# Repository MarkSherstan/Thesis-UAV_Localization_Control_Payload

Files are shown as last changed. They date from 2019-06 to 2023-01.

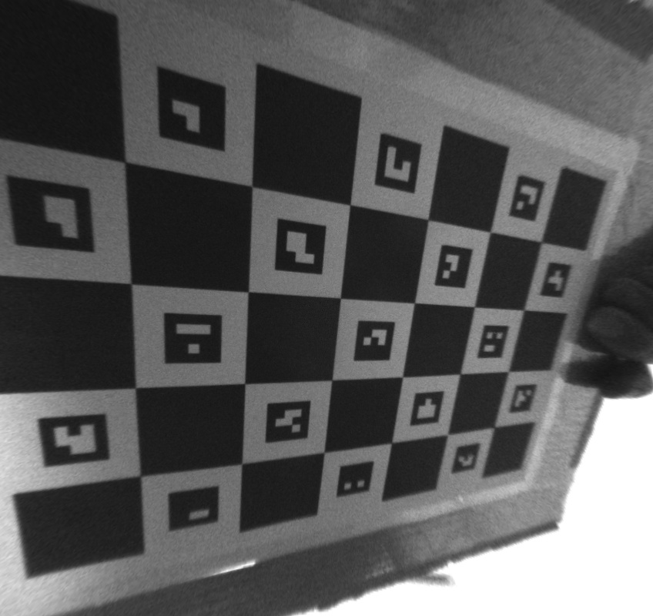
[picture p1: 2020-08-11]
control/cameraCalibration/calibrationImgs/Cam2/IMG_97.jpg

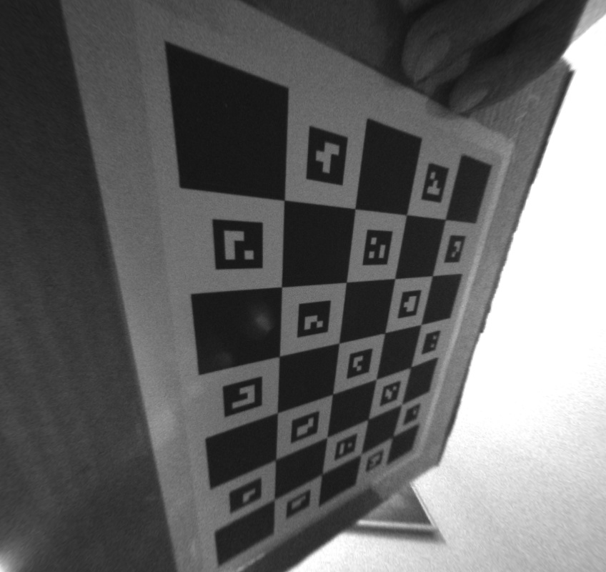
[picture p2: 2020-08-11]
control/cameraCalibration/calibrationImgs/Cam1/IMG_98.jpg

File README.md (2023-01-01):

# Thesis-UAV_Localization_Control_Payload
MSc thesis code for [Localization and Control of a Quadcopter Universal Payload System](https://era.library.ualberta.ca/items/3e5b67ea-13bb-48a5-877a-f02f7487af30).

## Abstract
There is a growing trend of using unmanned aerial vehicles (also known as UAVs, uncrewed aerial vehicles, or drones) to manipulate and interact with their surroundings. The algorithms and tools used are typically unique to the different tasks performed by UAVs; however, the fundamental UAV system largely remains consistent. This thesis offers a general quadrotor UAV system capable of performing multiple tasks dependent on available payloads. The system is empirically developed and performs localization using ArUco fiducial markers, an inertial measurement unit, and a Kalman filter. Navigation is achieved using a proportional integral derivative controller, and interfacing with various payloads is accomplished with a custom-developed universal payload manipulator. The system is described in detail and demonstrated with real-world experimentation, including the deployment of an example payload for removing twist caps off sump lubricant reservoirs. Empirical results show the developed system as an initial functional prototype in ideal conditions, and further work is required to increase system reliability and functionality for non-ideal scenarios.

## Setup
Clone the repo and install all the dependencies. For the first time call
`git submodule update --init --recursive`. Otherwise update using `git submodule update --recursive`.

Most of the developed code uses Python where a list of all the imported packages can be viewed in the below table. A majority of the Python packages come preinstalled; however, additional packages should be installed with `pip` (denoted with *). Two packages must be built directly from source code (denoted with **). All software ran on a Jetson Nano (quadcore ARM A57 processor) with Python 3.6.9 and Ubuntu 18.04.5 LTS.

| Package |Version | \| | Package |Version |
|---|---|----|---|---|
| datetime | 3.6.9  | \| | pymavlink* | 2.4.9  |
| DroneKit* | 2.9.2  | \| | pyrealsense2** | 2.36.0 |
| math | 3.6.9  | \| | pySerial* | 3.4 |
| Matplotlib* | 3.3.1  | \| | simdkalman* | 1.0.1  |
| multiprocessing | 3.6.9  | \| | statistics | 3.6.9  |
| NumPy* | 1.18.4 | \| | struct | 3.6.9  |
| openCV** | 4.3.0  | \| | threading | 3.6.9  |
| pandas* | 1.1.0  | \| | time | 3.6.9  |

For information regarding the building of non standard packages refer to the [wiki](https://github.com/MarkSherstan/UAV-Sampling-Control-System/wiki).
* [Build OpenCV](https://github.com/MarkSherstan/UAV-Sampling-Control-System/wiki/Build-OpenCV)
* [Build Pyrealsense2](https://github.com/MarkSherstan/UAV-Sampling-Control-System/wiki/Build-Pyrealsense2)

## Use  
Run the bash script `run.sh` and once the UAV is placed into `GUIDED_NOGPS` mode the UAV will be in full control. Use `control + c` to terminate the program and complete data logging.

## Flight Logs 
Flight logs are saved after each flight in `.csv` format. To plot data and analyze the log, navigate to the `/flightData` directory and enter the file name in the command line as such: `python3 plotter.py --input "flight1.csv"`.

## Payloads
Open the `/payloads` directory and navigate to either the `/cap` or `/MASTER` directory and build using PlatformIO. All pinout is labeled in `src/main.cpp`. The servo library may need to be re-installed with the following command: `pio lib install "Servo"` in the PlatformIO command line. Upload the compiled code to its respective PCB. 

## PCB
The PCB's were designed with [KiCad 5](https://kicad-pcb.org/download/) and manufactured by [JLCPCB](https://jlcpcb.com).

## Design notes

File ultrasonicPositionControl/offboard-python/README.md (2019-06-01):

# Off Board (Guided No GPS) Control Python
Python 2.7 is required. Python 3 and higher is not fully supported. The following packages should be installed (additional may be required, follow any errors generated).

```
sudo apt-get install python-lxml
pip install dronekit
pip install MAVProxy
pip install pymavlink
```

## Software In The Loop (SITL) Simulation
`dronekit-sitl` only has ArduCopter binaries up to version 3.3. As of May 2019 the ArduPilot GitHub repo has code up to 3.7-dev. Much of the current functionality from the new development is not captured in `dronekit-sitl` and therefore newer versions should be built to run an accurate simulation. The process outlined below primarily outlines the process for UNIX / MacOS operating systems, however links will be provided for other operating systems and more detailed instructions.

Start by cloning the [ArduPilot](https://github.com/ArduPilot/ardupilot) repo and navigate to new directory.

```
git clone https://github.com/ArduPilot/ardupilot.git
cd ardupilot/
```

Build the most up to date [binary](https://github.com/ArduPilot/ardupilot/blob/master/BUILD.md). Further information can be found as follows.
* [https://www.youtube.com/watch?v=PLGezPQYMrs&t=331s](https://www.youtube.com/watch?v=PLGezPQYMrs&t=331s)
* [https://www.youtube.com/watch?v=wLK2wLwEXm4&t=22s](https://www.youtube.com/watch?v=wLK2wLwEXm4&t=22s)
* [http://ardupilot.org/dev/docs/building-the-code.html](http://ardupilot.org/dev/docs/building-the-code.html)

```
git submodule update --init --recursive
./waf configure
./waf copter
```

Navigate to the following directory through the command line and run the simulator.

```
cd ardupilot/Tools/autotest
python sim_vehicle.py -v ArduCopter
```

Once the simulator is running. Open another command line and navigate to the following directory and run the program to test your control scheme.

```
cd UAV-Sampling-Control-System/ultrasonicPositionControl/offboard-python/
python main-SITL.py
```

## Off Board Interfacing
A [companion computer](http://ardupilot.org/dev/docs/companion-computers.html#companion-computers) is used to connect with the flight controller to implement off board control. Follow the guide for the respective hardware for setting up. To develop code connect on a desired serial port and use any of the commands outlined [here](https://web.archive.org/web/20180803235025/http://python.dronekit.io/guide/copter/guided_mode.html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).

Connect on `/dev/ttyS1` which are pins 8 and 10 on the J1 expansion connector of the Odroid C2. Further information can be found [here](https://wiki.odroid.com/odroid-c2/hardware/expansion_connectors) and a wiring diagram can be found [here](http://ardupilot.org/dev/_images/RaspberryPi_Pixhawk_wiring1.jpg) (RPi and Odroid C2 can be wired the same).

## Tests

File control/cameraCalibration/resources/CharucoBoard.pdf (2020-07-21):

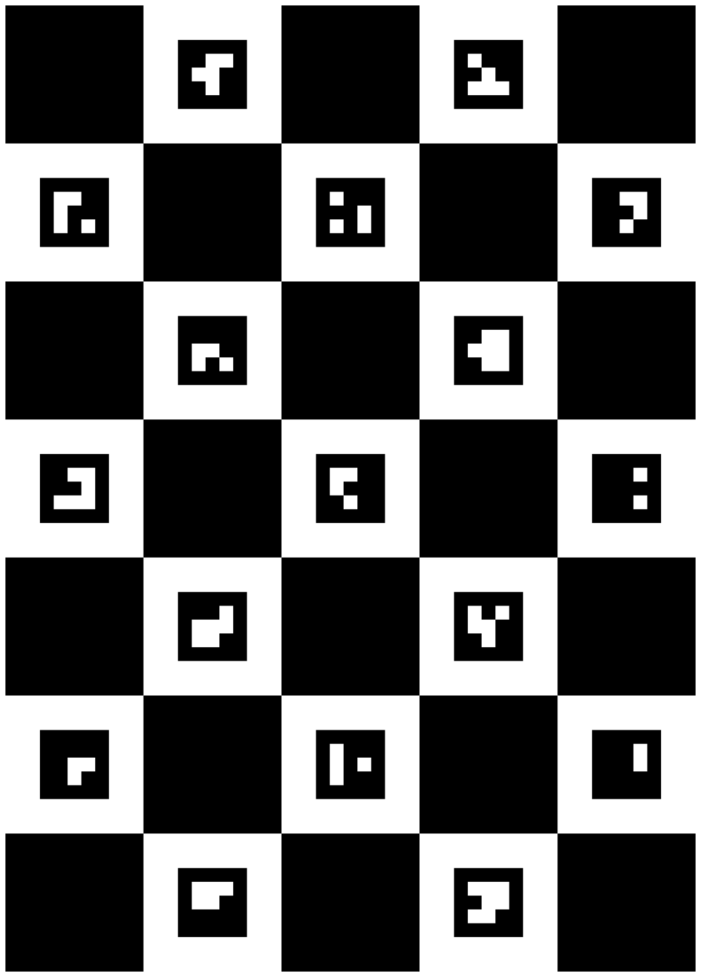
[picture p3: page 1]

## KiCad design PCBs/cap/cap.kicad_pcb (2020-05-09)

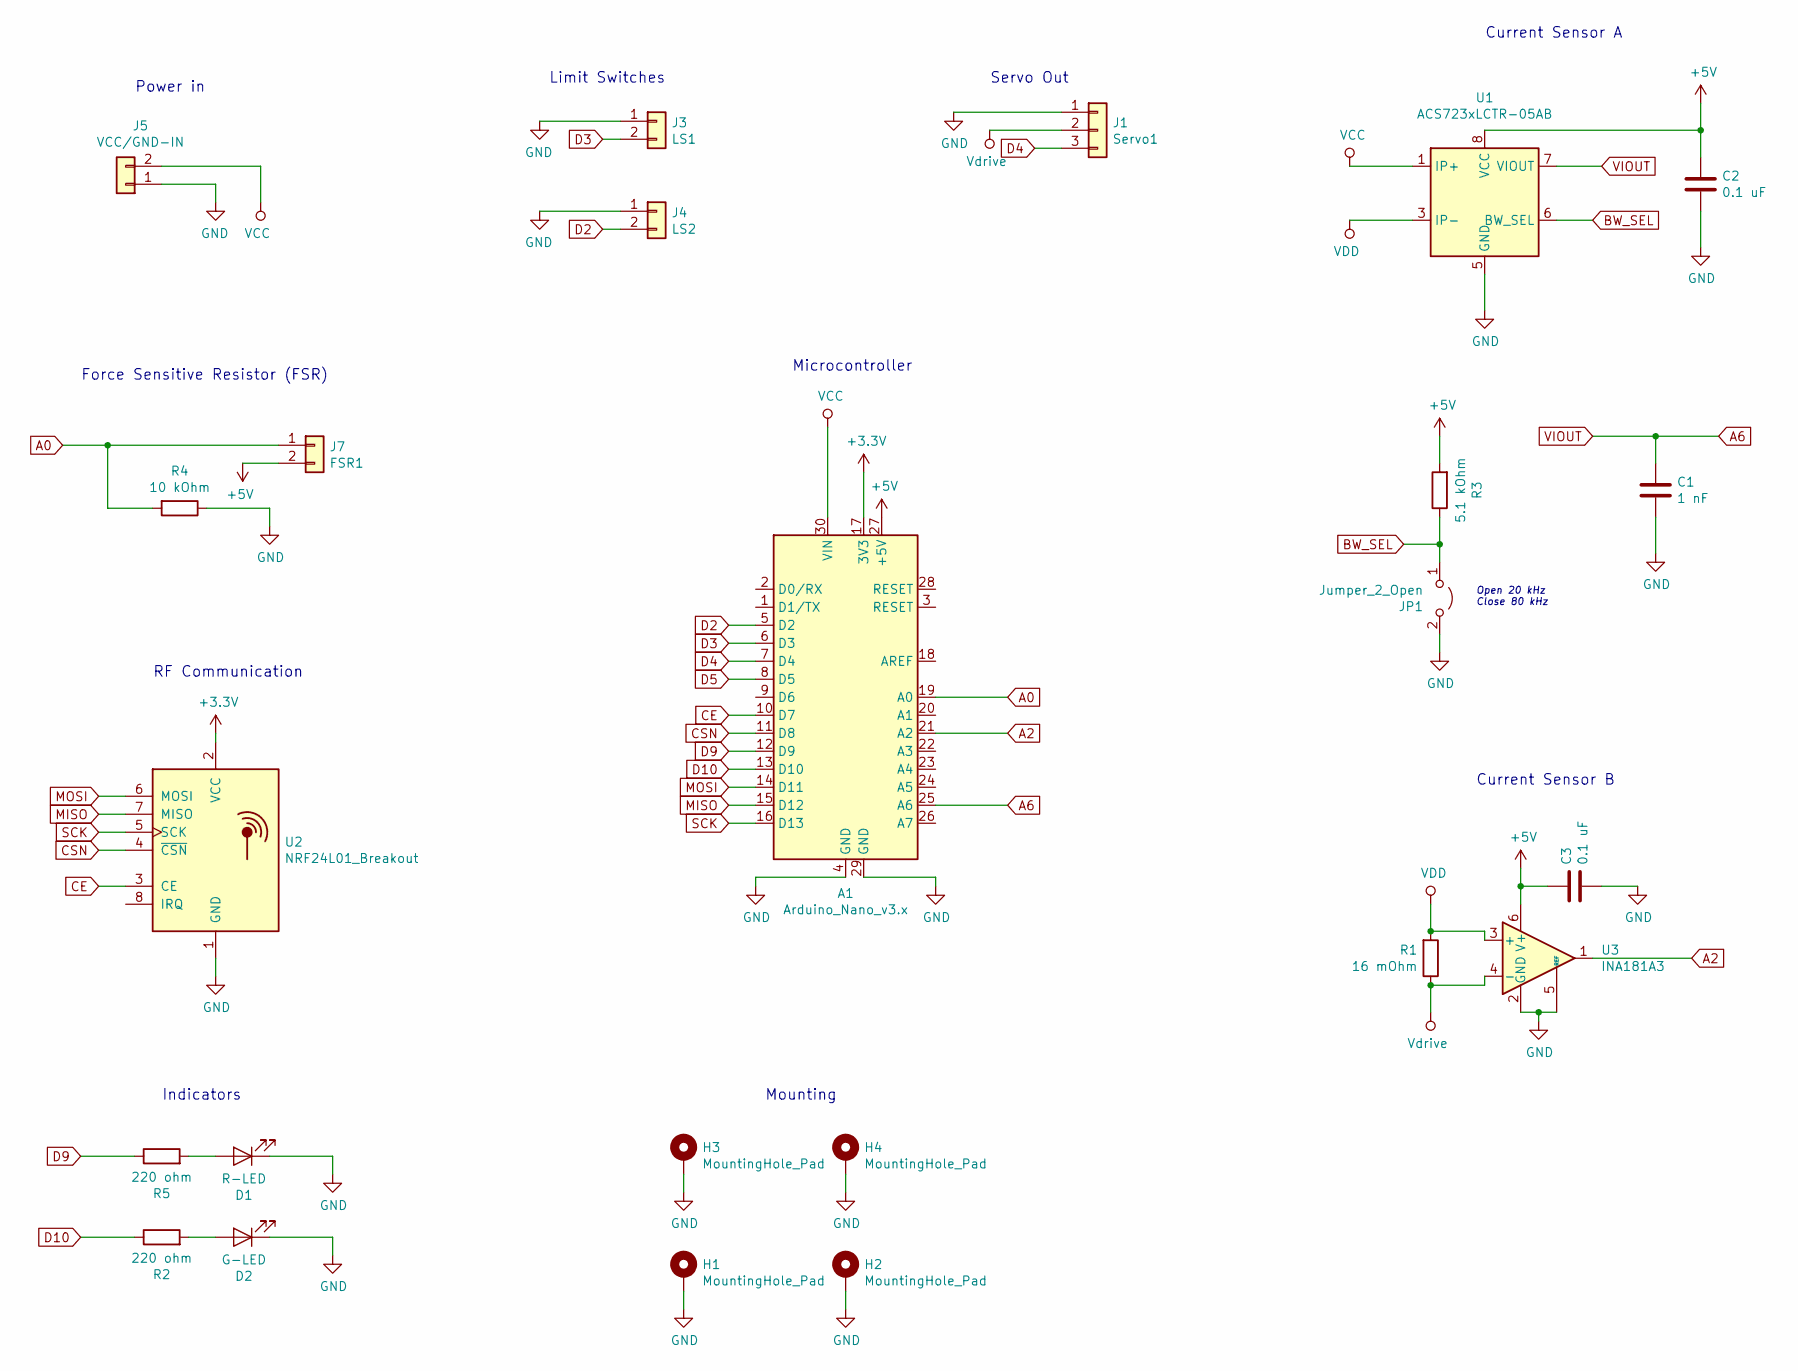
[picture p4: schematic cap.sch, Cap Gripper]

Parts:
A1: Arduino_Nano_v3.x; Arduino_Nano
C1: 1 nF; C_0603_1608Metric
C2, C3: 0.1 uF; C_0603_1608Metric
D1: R-LED; LED_0603_1608Metric_Pad1.05x0.95mm_HandSolder
D2: G-LED; LED_0603_1608Metric_Pad1.05x0.95mm_HandSolder
H1, H2, H3, H4: MountingHole_Pad; MountingHole_3.2mm_M3_ISO14580_Pad
J1: Servo1; Molex_Micro-Fit_3.0_43650-0300_1x03_P3.00mm_Horizontal
J3: LS1; Molex_Micro-Fit_3.0_43650-0200_1x02_P3.00mm_Horizontal
J4: LS2; Molex_Micro-Fit_3.0_43650-0200_1x02_P3.00mm_Horizontal
J5: VCC/GND-IN; Molex_Micro-Fit_3.0_43650-0200_1x02_P3.00mm_Horizontal
J7: FSR1; Molex_Micro-Fit_3.0_43650-0200_1x02_P3.00mm_Horizontal
JP1: Jumper_2_Open; SolderJumper-2_P1.3mm_Open_RoundedPad1.0x1.5mm
R1: 16 mOhm; R_1206_3216Metric_Pad1.42x1.75mm_HandSolder
R2, R5: 220 ohm; R_0603_1608Metric_Pad1.05x0.95mm_HandSolder
R3: 5.1 kOhm; R_0603_1608Metric
R4: 10 kOhm; R_0603_1608Metric
U1: ACS723xLCTR-05AB; SOIC-8_3.9x4.9mm_P1.27mm
U2: NRF24L01_Breakout; nRF24L01_Breakout
U3: INA181A3; SOT-23-6

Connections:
+3V3: A1.17 (3V3), U2.2 (VCC)
+5V: A1.27 (+5V), C2.1, C3.1, J7.2, R3.2, U1.8 (VCC), U3.6 (V+)
A0: A1.19 (A0), J7.1, R4.2
A2: A1.21 (A2), U3.1
A6: A1.25 (A6), C1.1, U1.7 (VIOUT)
BW_SEL: JP1.1 (A), R3.1, U1.6 (BW_SEL)
CE: A1.10 (D7), U2.3 (CE)
CSN: A1.11 (D8), U2.4 (~CSN)
D2: A1.5 (D2), J4.2
D3: A1.6 (D3), J3.2
D4: A1.7 (D4), J1.3
D9: A1.12 (D9), R5.1
D10: A1.13 (D10), R2.1
GND: A1.4 (GND), A1.29 (GND), C1.2, C2.2, C3.2, D1.1 (K), D2.1 (K), H1.1, H2.1, H3.1, H4.1, J1.1, J3.1, J4.1, J5.1, JP1.2 (B), R4.1, U1.5 (GND), U2.1 (GND), U3.2 (GND), U3.5 (REF)
MISO: A1.15 (D12), U2.7 (MISO)
MOSI: A1.14 (D11), U2.6 (MOSI)
unnamed: D1.2 (A), R5.2
unnamed: D2.2 (A), R2.2
SCK: A1.16 (D13), U2.5 (SCK)
VCC: A1.30 (VIN), J5.2, U1.1 (IP+), U1.2 (IP+)
VDD: R1.2, U1.3 (IP-), U1.4 (IP-), U3.3 (+)
Vdrive: J1.2, R1.1, U3.4 (-)

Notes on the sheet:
Current Sensor A
Open 20 kHz Close 80 kHz
Current Sensor B
Servo Out
Limit Switches
Force Sensitive Resistor (FSR)
Power in
Microcontroller
RF Communication
Indicators
Mounting

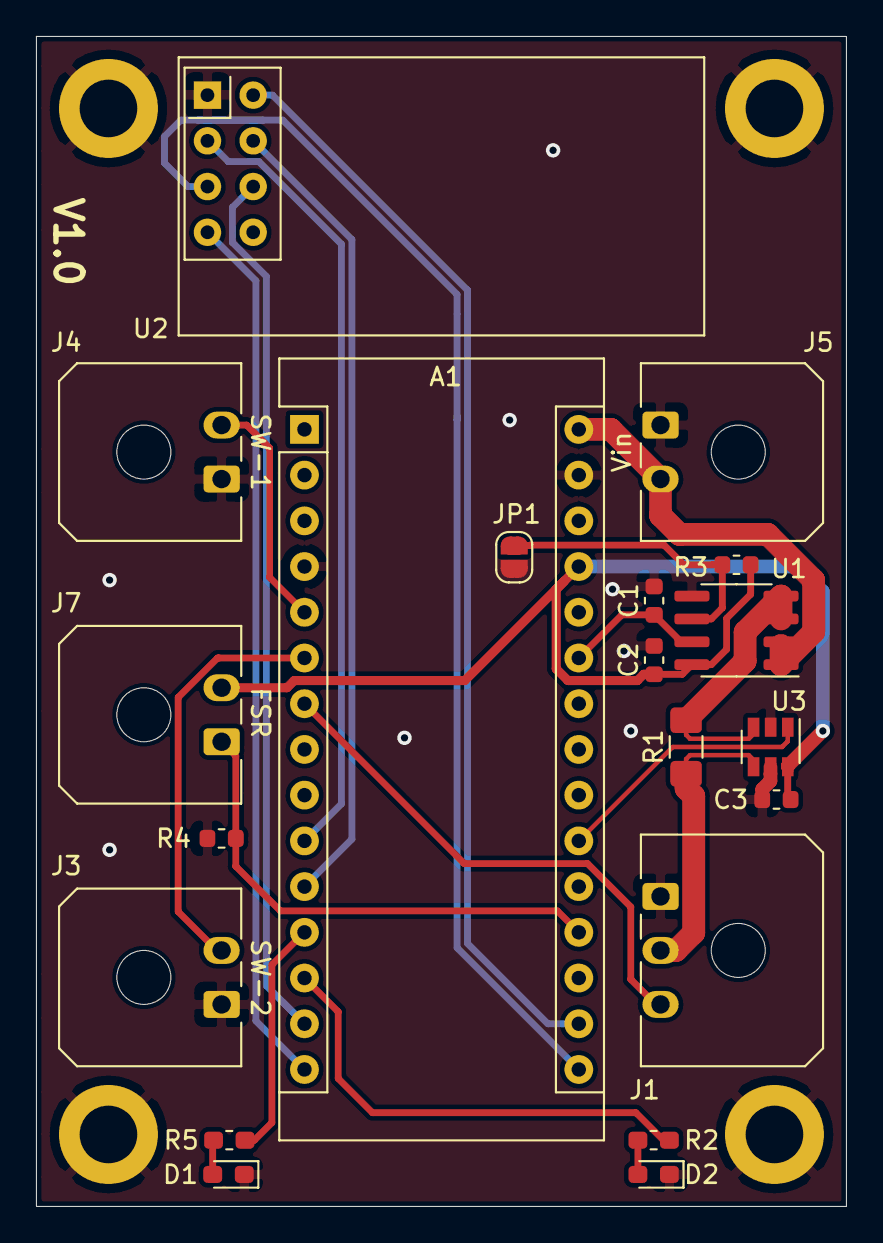
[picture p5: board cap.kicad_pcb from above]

Board: 2 copper layers, 45.0 x 65.0 mm, 24 parts (0 on the bottom side), 22 nets.

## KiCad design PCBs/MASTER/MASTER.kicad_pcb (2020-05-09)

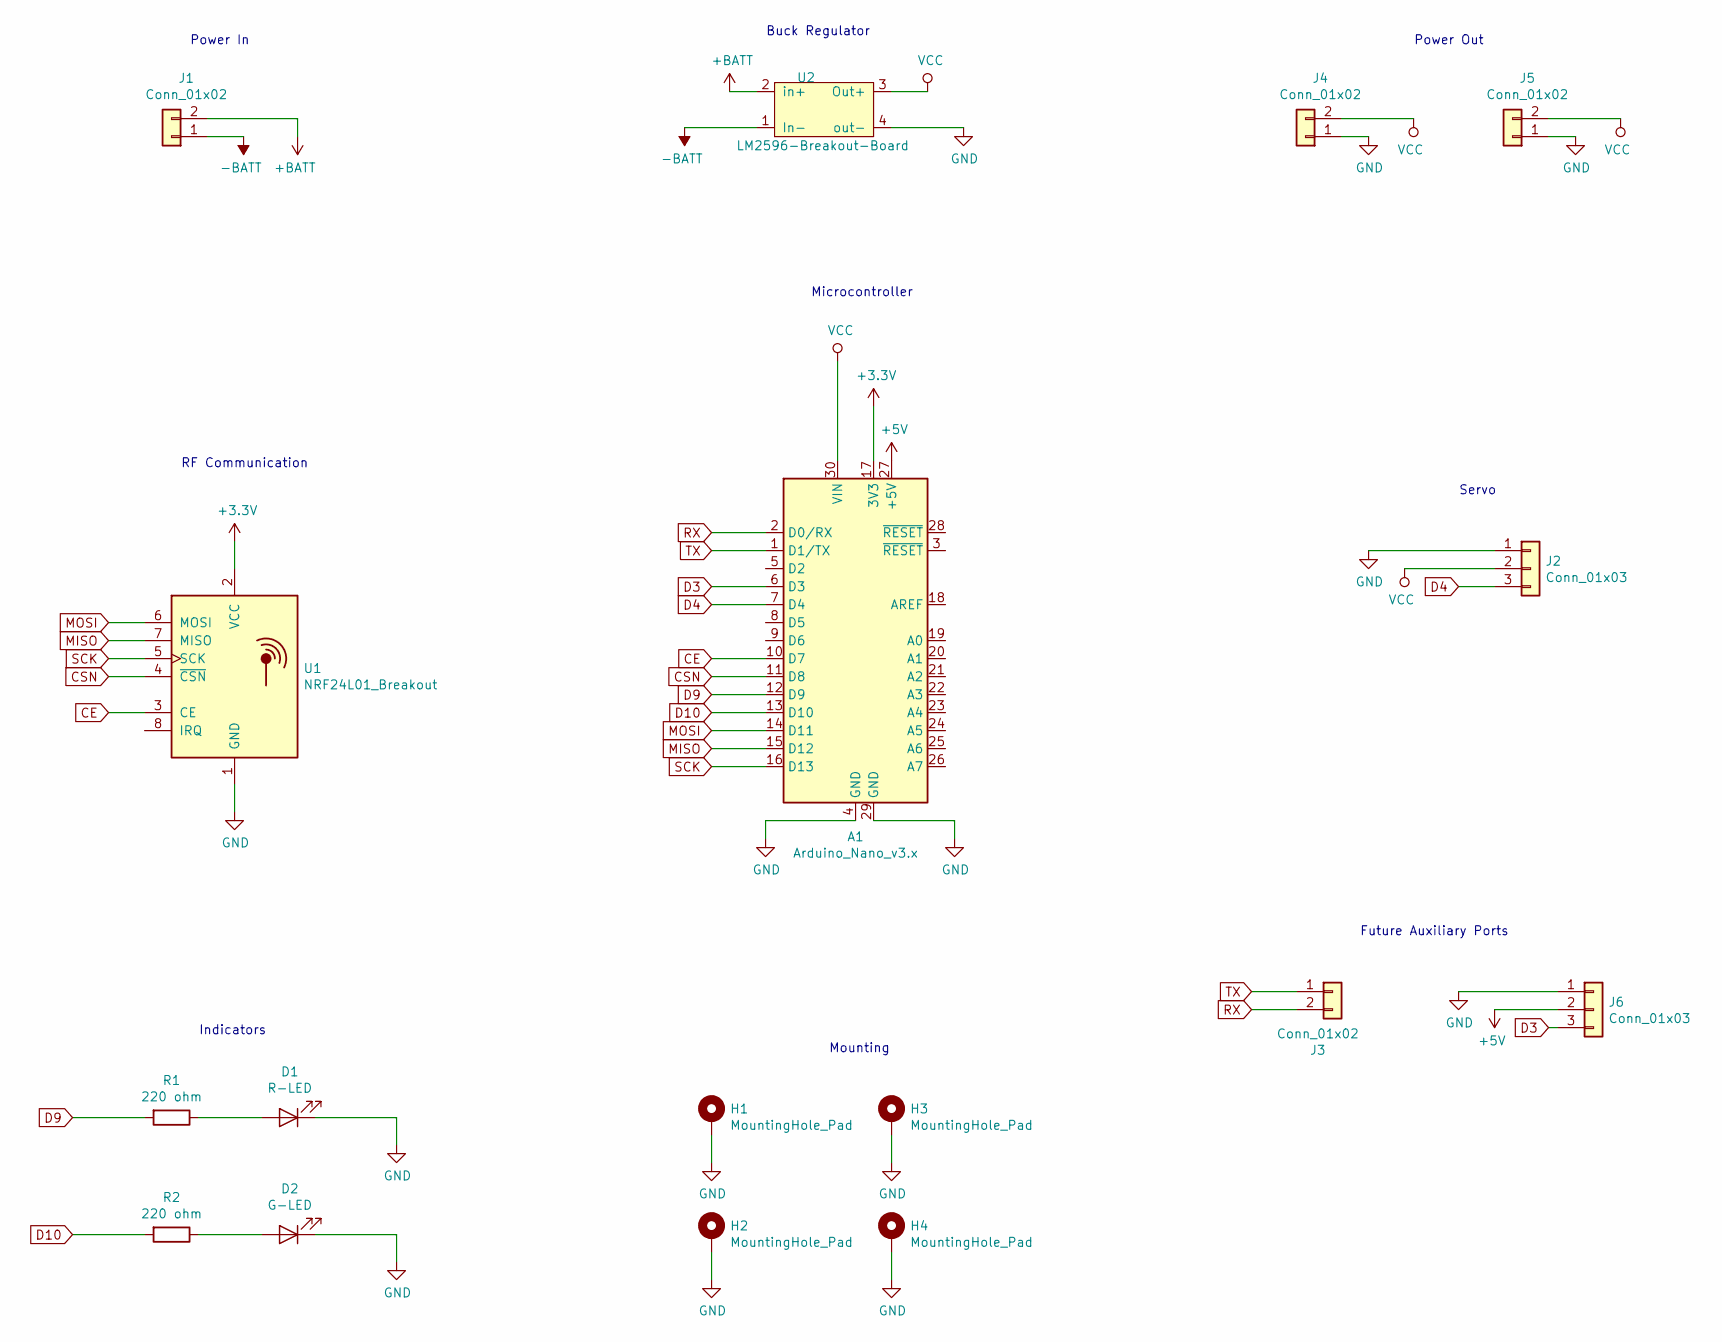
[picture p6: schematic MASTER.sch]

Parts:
A1: Arduino_Nano_v3.x; Arduino_Nano
D1: R-LED; LED_0603_1608Metric_Pad1.05x0.95mm_HandSolder
D2: G-LED; LED_0603_1608Metric_Pad1.05x0.95mm_HandSolder
H1, H2, H3, H4: MountingHole_Pad; MountingHole_3.2mm_M3_ISO14580_Pad
J1, J4, J5: Conn_01x02; Molex_Micro-Fit_3.0_43650-0200_1x02_P3.00mm_Horizontal
J2: Conn_01x03; Molex_Micro-Fit_3.0_43650-0300_1x03_P3.00mm_Horizontal
J3: Conn_01x02; PinHeader_1x02_P2.54mm_Vertical
J6: Conn_01x03; PinHeader_1x03_P2.54mm_Vertical
R1, R2: 220 ohm; R_0603_1608Metric_Pad1.05x0.95mm_HandSolder
U1: NRF24L01_Breakout; nRF24L01_Breakout
U2: LM2596-Breakout-Board

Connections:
+3V3: A1.17 (3V3), U1.2 (VCC)
+5V: A1.27 (+5V), J6.2
+BATT: J1.2, U2.2 (in+)
-BATT: J1.1, U2.1 (In-)
CE: A1.10 (D7), U1.3 (CE)
CSN: A1.11 (D8), U1.4 (~CSN)
D3: A1.6 (D3), J6.3
D4: A1.7 (D4), J2.3
D9: A1.12 (D9), R1.2
D10: A1.13 (D10), R2.2
GND: A1.4 (GND), A1.29 (GND), D1.1 (K), D2.1 (K), H1.1, H2.1, H3.1, H4.1, J2.1, J4.1, J5.1, J6.1, U1.1 (GND), U2.4 (out-)
MISO: A1.15 (D12), U1.7 (MISO)
MOSI: A1.14 (D11), U1.6 (MOSI)
unnamed: D1.2 (A), R1.1
unnamed: D2.2 (A), R2.1
RX: A1.2 (D0/RX), J3.2
SCK: A1.16 (D13), U1.5 (SCK)
TX: A1.1 (D1/TX), J3.1
VCC: A1.30 (VIN), J2.2, J4.2, J5.2, U2.3 (Out+)

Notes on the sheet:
Mounting
Indicators
RF Communication
Power In
Future Auxiliary Ports
Microcontroller
Servo
Power Out
Buck Regulator

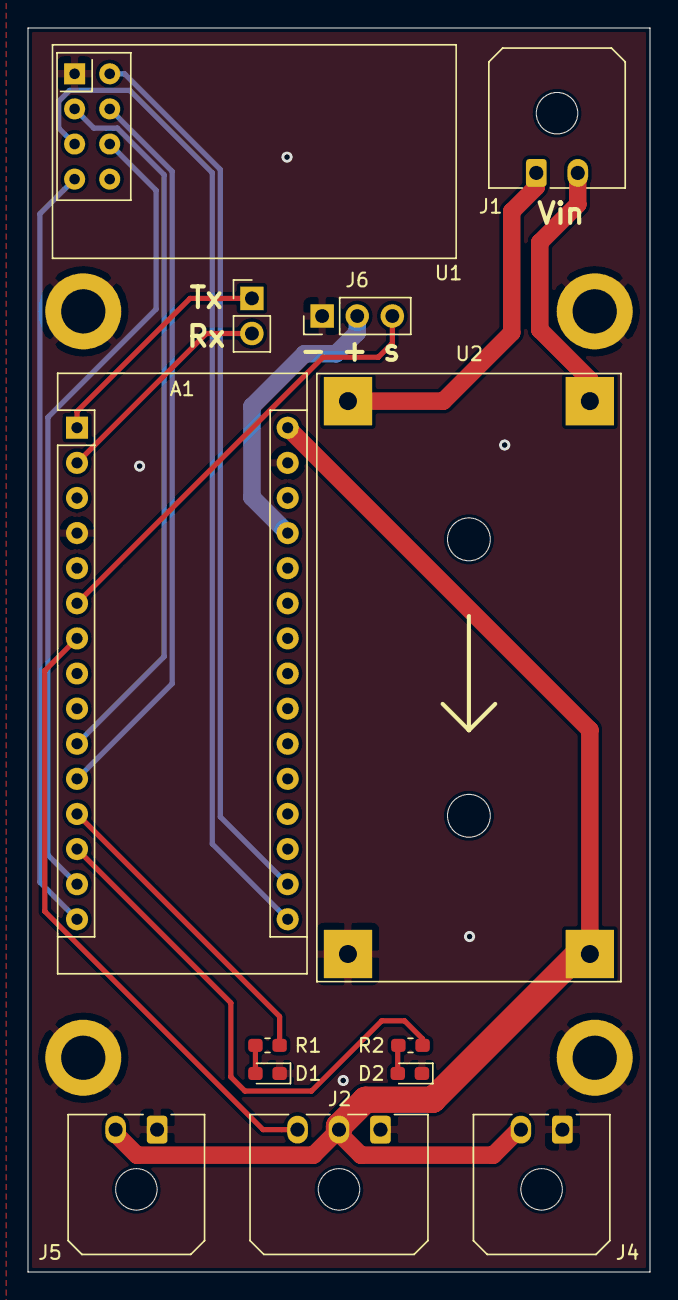
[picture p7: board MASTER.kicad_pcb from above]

Board: 2 copper layers, 45.0 x 90.0 mm, 17 parts (0 on the bottom side), 19 nets.

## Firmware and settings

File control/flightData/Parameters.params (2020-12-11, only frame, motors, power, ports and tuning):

1	1	ATC_ANGLE_BOOST	1	2
1	1	ATC_ANG_LIM_TC	1.000000000000000000	9
1	1	ATC_ANG_PIT_P	4.500000000000000000	9
1	1	ATC_ANG_RLL_P	4.500000000000000000	9
1	1	ATC_ANG_YAW_P	4.500000000000000000	9
1	1	ATC_RATE_FF_ENAB	1	2
1	1	ATC_RATE_P_MAX	0.000000000000000000	9
1	1	ATC_RATE_R_MAX	0.000000000000000000	9
1	1	ATC_RATE_Y_MAX	0.000000000000000000	9
1	1	ATC_RAT_PIT_D	0.003599999938160181	9
1	1	ATC_RAT_PIT_FF	0.000000000000000000	9
1	1	ATC_RAT_PIT_FLTD	20.000000000000000000	9
1	1	ATC_RAT_PIT_FLTE	0.000000000000000000	9
1	1	ATC_RAT_PIT_FLTT	20.000000000000000000	9
1	1	ATC_RAT_PIT_I	0.135000005364418030	9
1	1	ATC_RAT_PIT_IMAX	0.500000000000000000	9
1	1	ATC_RAT_PIT_P	0.135000005364418030	9
1	1	ATC_RAT_RLL_D	0.003599999938160181	9
1	1	ATC_RAT_RLL_FF	0.000000000000000000	9
1	1	ATC_RAT_RLL_FLTD	20.000000000000000000	9
1	1	ATC_RAT_RLL_FLTE	0.000000000000000000	9
1	1	ATC_RAT_RLL_FLTT	20.000000000000000000	9
1	1	ATC_RAT_RLL_I	0.135000005364418030	9
1	1	ATC_RAT_RLL_IMAX	0.500000000000000000	9
1	1	ATC_RAT_RLL_P	0.135000005364418030	9
1	1	ATC_RAT_YAW_D	0.000000000000000000	9
1	1	ATC_RAT_YAW_FF	0.000000000000000000	9
1	1	ATC_RAT_YAW_FLTD	0.000000000000000000	9
1	1	ATC_RAT_YAW_FLTE	2.000000000000000000	9
1	1	ATC_RAT_YAW_FLTT	20.000000000000000000	9
1	1	ATC_RAT_YAW_I	0.017999999225139618	9
1	1	ATC_RAT_YAW_IMAX	0.500000000000000000	9
1	1	ATC_RAT_YAW_P	0.180000007152557373	9
1	1	BATT2_MONITOR	0	2
1	1	BATT3_MONITOR	0	2
1	1	BATT4_MONITOR	0	2
1	1	BATT5_MONITOR	0	2
1	1	BATT6_MONITOR	0	2
1	1	BATT7_MONITOR	0	2
1	1	BATT8_MONITOR	0	2
1	1	BATT9_MONITOR	0	2
1	1	BATT_MONITOR	0	2
1	1	FLTMODE1	20	2
1	1	FLTMODE2	0	2
1	1	FLTMODE3	0	2
1	1	FLTMODE4	0	2
1	1	FLTMODE5	0	2
1	1	FLTMODE6	0	2
1	1	FLTMODE_CH	5	2
1	1	FRAME_CLASS	1	2
1	1	FRAME_TYPE	1	2
1	1	INS_GYRO_FILTER	40	4
1	1	INS_HNTCH_ENABLE	0	2
1	1	MOT_BAT_CURR_MAX	0.000000000000000000	9
1	1	MOT_BAT_CURR_TC	5.000000000000000000	9
1	1	MOT_BAT_IDX	0	2
1	1	MOT_BAT_VOLT_MAX	0.000000000000000000	9
1	1	MOT_BAT_VOLT_MIN	0.000000000000000000	9
1	1	MOT_BOOST_SCALE	0.000000000000000000	9
1	1	MOT_HOVER_LEARN	2	2
1	1	MOT_PWM_MAX	0	4
1	1	MOT_PWM_MIN	0	4
1	1	MOT_PWM_TYPE	0	2
1	1	MOT_SAFE_DISARM	0	2
1	1	MOT_SAFE_TIME	1.000000000000000000	9
1	1	MOT_SLEW_DN_TIME	0.000000000000000000	9
1	1	MOT_SLEW_UP_TIME	0.000000000000000000	9
1	1	MOT_SPIN_ARM	0.100000001490116119	9
1	1	MOT_SPIN_MAX	0.949999988079071045	9
1	1	MOT_SPIN_MIN	0.170000001788139343	9
1	1	MOT_SPOOL_TIME	0.500000000000000000	9
1	1	MOT_THST_EXPO	0.649999976158142090	9
1	1	MOT_THST_HOVER	0.518168509006500244	9
1	1	MOT_YAW_HEADROOM	200	4
1	1	SERIAL0_BAUD	115	6
1	1	SERIAL0_PROTOCOL	2	2
1	1	SERIAL1_BAUD	57	6
1	1	SERIAL1_OPTIONS	0	4
1	1	SERIAL1_PROTOCOL	1	2
1	1	SERIAL2_BAUD	1500	6
1	1	SERIAL2_OPTIONS	0	4
1	1	SERIAL2_PROTOCOL	2	2
1	1	SERIAL3_BAUD	38	6
1	1	SERIAL3_OPTIONS	0	4
1	1	SERIAL3_PROTOCOL	5	2
1	1	SERIAL4_BAUD	38	6
1	1	SERIAL4_OPTIONS	0	4
1	1	SERIAL4_PROTOCOL	5	2
1	1	SERIAL5_BAUD	57	6
1	1	SERIAL5_OPTIONS	0	4
1	1	SERIAL5_PROTOCOL	-1	2
1	1	SERIAL6_BAUD	57	6
1	1	SERIAL6_OPTIONS	0	4
1	1	SERIAL6_PROTOCOL	-1	2
1	1	SERIAL7_BAUD	115200	6
1	1	SERIAL7_OPTIONS	0	4
1	1	SERIAL7_PROTOCOL	2	2
1	1	SERVO1_FUNCTION	33	4
1	1	SERVO1_MAX	1900	4
1	1	SERVO1_MIN	1100	4
1	1	SERVO1_REVERSED	0	2
1	1	SERVO1_TRIM	1500	4
1	1	SERVO2_FUNCTION	34	4
1	1	SERVO2_MAX	1900	4
1	1	SERVO2_MIN	1100	4
1	1	SERVO2_REVERSED	0	2
1	1	SERVO2_TRIM	1500	4
1	1	SERVO3_FUNCTION	35	4
1	1	SERVO3_MAX	1900	4
1	1	SERVO3_MIN	1100	4
1	1	SERVO3_REVERSED	0	2
1	1	SERVO3_TRIM	1500	4
1	1	SERVO4_FUNCTION	36	4
1	1	SERVO4_MAX	1900	4
1	1	SERVO4_MIN	1100	4
1	1	SERVO4_REVERSED	0	2
1	1	SERVO4_TRIM	1500	4
1	1	SERVO5_FUNCTION	0	4
1	1	SERVO5_MAX	1900	4
1	1	SERVO5_MIN	1100	4
1	1	SERVO5_REVERSED	0	2
1	1	SERVO5_TRIM	1500	4
1	1	SERVO6_FUNCTION	0	4
1	1	SERVO6_MAX	1900	4
1	1	SERVO6_MIN	1100	4
1	1	SERVO6_REVERSED	0	2
1	1	SERVO6_TRIM	1500	4
1	1	SERVO7_FUNCTION	0	4
1	1	SERVO7_MAX	1900	4
1	1	SERVO7_MIN	1100	4
1	1	SERVO7_REVERSED	0	2
1	1	SERVO7_TRIM	1500	4
1	1	SERVO8_FUNCTION	0	4
1	1	SERVO8_MAX	1900	4
1	1	SERVO8_MIN	1100	4
1	1	SERVO8_REVERSED	0	2
1	1	SERVO8_TRIM	1500	4
1	1	SERVO9_FUNCTION	0	4
1	1	SERVO9_MAX	1900	4
1	1	SERVO9_MIN	1100	4
1	1	SERVO9_REVERSED	0	2
1	1	SERVO9_TRIM	1500	4

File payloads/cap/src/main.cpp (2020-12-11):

#include <Arduino.h>
#include <Servo.h>
#include <RF24Network.h>
#include <RF24.h>
#include <SPI.h>
#include "capPayload.h"

// Pinout Analog
#define forceAnalog         0
#define currentHallAnalog   6
#define currentOpAmpAnalog  2

// Pinout Digital
#define limitSwitchA    2
#define limitSwitchB    3
#define clampServo      4
#define radioCE         7
#define radioCSN        8
#define rLED            9
#define gLED            10

// Servo pulses, threshold, and timer
#define clampOpen         2000
#define clampClose        1000
#define clampStop         1520
#define forceThresh       150
#define currentThresh     300
#define loopTimeMicroSec  10000

// Variables
float force, forceDesL, forceDesH, current;
bool switchStateA, switchStateB;
byte dataIn, dataOut;
int servoControl;

// Setup classes
CapPayload CP;
Servo clamp;
RF24 radio(radioCE, radioCSN);
RF24Network network(radio);

// Functions
void sendMessage(byte dataOut);
void receiveMessage();
void boundaryControl();
void calibrate();
void close();
void open();

// Run once
void setup(){
  // Configure digital pins
  CP.setUpDigitalPins(limitSwitchA, limitSwitchB, rLED, gLED);

  // Set up clamping servo and set to off
  clamp.attach(clampServo);
  clamp.writeMicroseconds(clampStop);

  // Set up radio and network
  SPI.begin();
  radio.begin();
  network.begin(CHANNEL, THIS_NODE);
  radio.setDataRate(RF24_2MBPS);

  // Start time sync (10000->100Hz, 5000->200Hz)
  CP.startTimeSync(loopTimeMicroSec);

  // Calibration streaming function
  // calibrate();
}

// Run forever
void loop(){
  // Check for incoming message
  receiveMessage();

  // Use incoming byte to determine state
  switch(dataIn) {
    case CLOSE:
      close();
      break;

    case OPEN:
      open();
      break;

    default:
      boundaryControl();
      clamp.write(clampStop);
      sendMessage(FLOATING);
      break;
  }

  // Stabilize sampling rate
  CP.timeSync();
}

void sendMessage(byte dataOut){
    // Send message
    RF24NetworkHeader header(MASTER_NODE);
    network.write(header, &dataOut, sizeof(dataOut));
}

void receiveMessage(){
  // Update the network
  network.update();

  // Receiving data if available
  while (network.available()){
    RF24NetworkHeader header;
    network.read(header, &dataIn, sizeof(dataIn));
  }
}

void boundaryControl(){
  // Get limit switch reading
  switchStateA = CP.readSwitch(limitSwitchA);
  switchStateB = CP.readSwitch(limitSwitchB);

  // Open or close the jaws based on the response
  if (switchStateA == 0){
    clamp.writeMicroseconds(clampOpen);
    CP.LED_ON(rLED);
    delay(500);
    CP.LED_OFF(rLED);
  } else if (switchStateB == 0){
    clamp.writeMicroseconds(clampClose);
    CP.LED_ON(rLED);
    delay(500);
    CP.LED_OFF(rLED);
  }
}

void close(){
  while(true){
    // Close the clamps
    clamp.writeMicroseconds(clampClose);

    // Not yet closed
    sendMessage(FLOATING);

    // Check if there is an updated command
    receiveMessage();
    if (dataIn == OPEN){
      break;
    }

    // Beware of limit switches
    boundaryControl();

    // Acquire new data from onboard sensors
    force = CP.readFSR(forceAnalog);
    current = CP.readCurrent(currentHallAnalog, currentOpAmpAnalog);

    // If thresholds are met keep clamped
    if ((force >= forceThresh) && (current >= currentThresh)) {
      // Turn on LED
      CP.LED_ON(gLED);

      // Send clamped message
      sendMessage(CLAMPED);

      // Update control variables
      forceDesH = force * 1.3;
      forceDesL = force * 1;
      servoControl = clampStop;

      while(true){
        // Beware of limit switches
        boundaryControl();

        // Get fresh force data
        force = CP.readFSR(forceAnalog);

        // Do some control for clamping force
        if (force >= forceDesH){
          servoControl += 1;
        } else if (force <= forceDesL){
          servoControl -= 1;
        }

        servoControl = constrain(servoControl, clampClose, clampOpen);

        // Send the servo command
        clamp.writeMicroseconds(servoControl);

        // Update message
        sendMessage(CLAMPED);

        // Can the cap be released?
        receiveMessage();
        if (dataIn == OPEN){
          CP.LED_OFF(gLED);
          break;
        }

        // Stabilize sampling rate
        CP.timeSync();
      }
    }

    // Stabilize sampling rate
    CP.timeSync();
  }

  // Stop the clamp and break
  clamp.write(clampStop); 
}

void open(){
  while(CP.readSwitch(limitSwitchB) != 0){
    // Turn on LED 
    CP.LED_ON(gLED);

    // Open the clamp
    clamp.writeMicroseconds(clampOpen);

    // Check if there is an updated command
    receiveMessage();
    if (dataIn == CLOSE){
      break;
    }

    // Get fresh force data
    force = CP.readFSR(forceAnalog);

    // Check if released and send corresponding message
    if (force < 5){
      sendMessage(RELEASED);
    } else {
      sendMessage(FLOATING);
    }

    // Stabilize sampling rate
    CP.timeSync();
  }

  // Stop the clamp, turn off LED, and break
  clamp.write(clampStop);
  CP.LED_OFF(gLED);
}

void calibrate(){
  // Start a serial port
  Serial.begin(9600);
  unsigned long now = micros();

  while(true){
    // Beware of limit switches
    boundaryControl();

    // Print current and FSR values
    now = micros();
    Serial.print(now); Serial.print(",");
    current = CP.readCurrent(currentHallAnalog, currentOpAmpAnalog, true);
    force = CP.readFSR(forceAnalog);
    Serial.println(force);

    // Stabilize sampling rate
    CP.timeSync();
  }
}

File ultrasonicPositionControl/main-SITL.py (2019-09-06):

from dronekit import connect, VehicleMode, LocationGlobal, LocationGlobalRelative, LocationLocal
from pymavlink import mavutil
import matplotlib.pyplot as plt
import numpy as np
import pandas as pd
import matplotlib
import datetime
import time
import math
import random

class Simulate:
    def __init__(self):
        self.vehicleArmed = True
        self.vehicleMode = "GUIDED" #GUIDED_NOGPS wont display position for simulating

    def armAndTakeOff(self, C, vehicle, targetAltitude):
        # Give the user some info
        print("Basic pre-arm checks")
        print("--------------------------------------------------")

        # Wait till vehicle is ready
        while not vehicle.is_armable:
            print(" Waiting for vehicle to initialize...")
            time.sleep(1)

        print("Arming motors")

        # Set vehicle mode
        vehicle.mode = VehicleMode(self.vehicleMode)
        vehicle.armed = self.vehicleArmed

        # Arm the vehicle
        while not vehicle.armed:
            print(" Waiting for arming...")
            vehicle.armed = self.vehicleArmed
            time.sleep(1)

        # Take off
        print("Taking off!")
        print("--------------------------------------------------")

        # Send take off command
        vehicle.simple_takeoff(targetAltitude)

        # Wait until actual altitude is achieved
        while abs(vehicle.location.local_frame.down) <= targetAltitude:
            print '  ', round(vehicle.location.local_frame.down,3)
            time.sleep(0.2)

        # Small pause and display message
        time.sleep(0.5)
        print '\nAltitude achieved\n'

        # double check the yaw is aligned
        while not ((358 <= vehicle.heading <= 360) or (0 <= vehicle.heading <= 2)):
            C.sendAttitudeTarget(vehicle)
            print '  ', vehicle.heading
            time.sleep(0.1)

        # Small pause and display message
        time.sleep(0.5)
        print '\nYaw achieved\n'

class Controller:
    def __init__(self):
        # Initial conditions (rads)
        self.rollAngle = 0.0
        self.pitchAngle = 0.0
        self.yawAngle = 0.0
        self.yawRate = 0.0
        self.thrust = 0.5
        self.duration = 0.08

        # Constraints for roll, pitch, and thrust
        self.minValNE = -3.1415/8
        self.maxValNE = 3.1415/8
        self.minValD = -1
        self.maxValD = 1

        # PID Controller Gains
        self.kp = 0.3
        self.ki = 0
        self.kd = 0.2

        # PID variables
        self.northPreviousError = 0
        self.eastPreviousError = 0
        self.northI = 0
        self.eastI = 0

        # Controller
        self.northDesired = None
        self.eastDesired = None
        self.downDesired = None
        self.startTime = None

        # Thrust Control
        self.kThrottle = 0.5
        self.one2one = [-1,0,1]
        self.zero2one = [0, 0.5, 1]

        # Save values for plotting
        self.northDesiredList = []
        self.northActualList = []
        self.eastDesiredList = []
        self.eastActualList = []
        self.downDesiredList = []
        self.downActualList = []
        self.rollList = []
        self.pitchList = []
        self.timeList = []

    def sendAttitudeTarget(self, vehicle):
		# https://mavlink.io/en/messages/common.html#SET_ATTITUDE_TARGET
		#
		# useYawRate: the yaw can be controlled using yawAngle OR yawRate.
		#
		# thrust: 0 <= thrust <= 1, as a fraction of maximum vertical thrust.
		#         Note that as of Copter 3.5, thrust = 0.5 triggers a special case in
		#         the code for maintaining current altitude.
		#             Thrust >  0.5: Ascend
		#             Thrust == 0.5: Hold the altitude
		#             Thrust <  0.5: Descend
		#
		# Mappings: If any of these bits are set, the corresponding input should be ignored.
		# bit 1: body roll rate, bit 2: body pitch rate, bit 3: body yaw rate.
		# bit 4-bit 6: reserved, bit 7: throttle, bit 8: attitude

		# Create the mavlink message
		msg = vehicle.message_factory.set_attitude_target_encode(
			0, # time_boot_ms
			0, # Target system
			0, # Target component
			0b00000100, # If bit is set corresponding input ignored (mappings)
			self.euler2quaternion(self.rollAngle, self.pitchAngle, self.yawAngle), # Quaternion
			0, # Body roll rate in radian
			0, # Body pitch rate in radian
			self.yawRate, # Body yaw rate in radian/second
			self.thrust # Thrust
		)

		# Send the constructed message
		vehicle.send_mavlink(msg)

    def euler2quaternion(self, roll, pitch, yaw):
        # Euler angles (rad) to quaternion
        yc = math.cos(yaw * 0.5)
        ys = math.sin(yaw * 0.5)
        rc = math.cos(roll * 0.5)
        rs = math.sin(roll * 0.5)
        pc = math.cos(pitch * 0.5)
        ps = math.sin(pitch * 0.5)

        q0 = yc * rc * pc + ys * rs * ps
        q1 = yc * rs * pc - ys * rc * ps
        q2 = yc * rc * ps + ys * rs * pc
        q3 = ys * rc * pc - yc * rs * ps

        return [q0, q1, q2, q3]

    def constrain(self, val, minVal, maxVal):
        return max(min(maxVal, val), minVal)

    def PID(self, error, errorPrev, I, dt):
        # Run the PD controller
        P = self.kp * error
        I = self.ki * (I + error * dt)
        D = self.kd * ((error - errorPrev) / dt)
        return (P + I + D), I

    def northEastTest(self, vehicle):
        # Run for 10 seconds
        while (time.time() < self.startTime + 10):

            # Get current values
            northCurrentPos = vehicle.location.local_frame.north
            eastCurrentPos = vehicle.location.local_frame.east
            deltaT = time.time() - self.startTime

            # Save values for plotting
            self.northDesiredList.append(self.northDesired)
            self.northActualList.append(northCurrentPos)
            self.eastDesiredList.append(self.eastDesired)
            self.eastActualList.append(eastCurrentPos)
            self.timeList.append(deltaT)

            # Error caculations
            errorNorth = northCurrentPos - self.northDesired
            errorEast = eastCurrentPos - self.eastDesired

            # Update previous position(s) if none
            if self.northPreviousPos is None:
                self.northPreviousPos = northCurrentPos

            if self.eastPreviousPos is None:
                self.eastPreviousPos = eastCurrentPos

            # Run PD control
            pitchControl = self.PD(errorNorth, northCurrentPos, self.northPreviousPos, deltaT)
            rollControl = self.PD(errorEast, eastCurrentPos, self.eastPreviousPos, deltaT)

            # Save the previous position
            self.northPreviousPos = northCurrentPos
            self.eastPreviousPos = eastCurrentPos

            # Execute the controller and print results
            self.pitchAngle = self.constrain(pitchControl, self.minValNE, self.maxValNE)
            self.rollAngle = self.constrain(-rollControl, self.minValNE, self.maxValNE)
            self.setAttitude(vehicle)
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

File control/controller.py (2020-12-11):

from filter import MovingAverage
import pandas as pd
import datetime
import time
import math

class Controller:
    def __init__(self, vehicle):
        # Vehicle class
        self.UAV = vehicle

        # Maximum controller output constraints
        self.rollConstrain  = [-4, 4]               # Deg
        self.pitchConstrain = self.rollConstrain    # Deg
        self.thrustConstrain = [-0.5, 0.5]	        # Normalized
        self.yawRateConstrain = [-10, 10]           # Deg / s
        self.derivativeGainConstrain = [-125, 125]  # [ ]

        # PID Gains: NORTH (pitch)
        self.kp_NORTH = 0.17
        self.ki_NORTH = 0.015   # Max 3 deg with 200 bounds
        self.kd_NORTH = 0.08

        # PID Gains: EAST (roll)
        self.kp_EAST = 0.16
        self.ki_EAST = 0.015    # Max 3 deg with 200 bounds
        self.kd_EAST = 0.11

        # PID Gains: DOWN (thrust)
        self.kp_DOWN = 0.002
        self.ki_DOWN = 0.00008   # Max 0.04 with 500 bounds
        self.kd_DOWN = 0

        # PID Gains: YAW (yaw rate)
        self.kp_YAW = 0.20
        self.ki_YAW = 0.02
        self.kd_YAW = 0.00

        # Cutoff height
        self.gainHeight = 25.0
        
        # Landing check 
        self.landErrorNE = 5.0
        self.landErrorD  = 10.0
        self.landHeight  = 15.0
        self.landCount   = 0 
        self.landCountRequired = 45

        # Previous errors
        self.northPrevError = 0
        self.eastPrevError = 0
        self.downPrevError = 0
        self.yawPrevError = 0

        # Integral tracking
        self.northI = 0
        self.eastI = 0
        self.downI = 0
        self.yawI = 0

        # Integral term constraints
        self.northIcontstrain = [-200, 200]
        self.eastIcontstrain  = self.northIcontstrain
        self.downIcontstrain  = [-500, 500]
        self.yawIcontstrain   = [-500, 500]

        # Timing
        self.timer = None

        # Data logging
        self.tempData = []
        self.data = []
        
        # Low pass filter for D term
        self.nAvg = MovingAverage(5)
        self.eAvg = MovingAverage(5)
        self.dAvg = MovingAverage(5)
        self.yAvg = MovingAverage(5)
        
    def startController(self):
        self.resetController()
        self.sendAttitudeTarget(0, 0, 0, 0.5)
        self.timer = time.time()
        self.startTime = time.time()

    def resetController(self):
        # Reset integral terms
        self.northI = 0
        self.eastI = 0
        self.downI = 0
        self.yawI = 0
        
        # Reset landing counter 
        self.landCount = 0
        
        # Reset timer 
        self.timer = time.time()

    def euler2quaternion(self, roll, pitch, yaw):
        # Convert degrees to radians 
        roll = math.radians(roll)
        pitch = math.radians(pitch)
        yaw = math.radians(yaw)
        
        # Euler angles (rad) to quaternion
        yc = math.cos(yaw * 0.5)
        ys = math.sin(yaw * 0.5)
        rc = math.cos(roll * 0.5)
        rs = math.sin(roll * 0.5)
        pc = math.cos(pitch * 0.5)
        ps = math.sin(pitch * 0.5)

        q0 = yc * rc * pc + ys * rs * ps
        q1 = yc * rs * pc - ys * rc * ps
        q2 = yc * rc * ps + ys * rs * pc
        q3 = ys * rc * pc - yc * rs * ps

        return [q0, q1, q2, q3]

    def sendAttitudeTarget(self, roll, pitch, yawRate, thrustRate):
        # Convert from degrees to radians
        yawRate = math.radians(yawRate)

        # https://mavlink.io/en/messages/common.html#SET_ATTITUDE_TARGET
        # https://ardupilot.org/dev/docs/copter-commands-in-guided-mode.html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
        msg = self.UAV.message_factory.set_attitude_target_encode(
            0, # time_boot_ms
            0, # Target system
            0, # Target component
            0b00000000, # If bit is set corresponding input ignored (mappings)
            self.euler2quaternion(roll, pitch, 0), # Quaternion
            0, # Body roll rate in radian
            0, # Body pitch rate in radian
            yawRate,   # Body yaw rate in rad/s
            thrustRate # Thrust
        )
        
        # Send the constructed message
        self.UAV.send_mavlink(msg)

    def getVehicleAttitude(self):
        # Actual vehicle attitude
        roll  = math.degrees(self.UAV.attitude.roll)
        pitch = math.degrees(self.UAV.attitude.pitch)
        yaw   = math.degrees(self.UAV.attitude.yaw)
        return roll, pitch, yaw
       
    def constrain(self, val, minVal, maxVal):
        return max(min(maxVal, val), minVal)

    def PID(self, error, errorPrev, I, dt, kp, ki, kd, filt, debug=False):
        # Run the PID controller
        P = error
        I = I + error * dt
        D = filt.update(self.constrain((error - errorPrev) / dt, self.derivativeGainConstrain[0], self.derivativeGainConstrain[1]))
        PID = (kp * P) + (ki * I) + (kd * D)

        # Logging
        self.tempData.extend([kp, ki, kd, I, P*kp, I*ki, D*kd, (PID)])
        
        # Debugging
        if debug is True:
            print('{:<8.0f} {:<8.0f} {:<8.0f} {:<8.2f} {:<8.2f} {:<8.2f} {:<8.2f}'.format(error, 1/dt, I, P*kp, I*ki, D*kd, (PID)))
        
        # Return values 
        return PID, I

    def positionControl(self, actual, desired):
        # Error calculations
        errorNorth = desired[0] - actual[0]
        errorEast  = desired[1] - actual[1]
        errorDown  = desired[2] - actual[2]
        errorYaw   = desired[3] - actual[3]

        # Get time delta
        dt = time.time() - self.timer
        self.timer = time.time()
            
        # Run the remainder of the control
        rollControl, self.eastI   = self.PID(errorEast, self.eastPrevError, self.eastI, dt, self.kp_EAST, self.ki_EAST, self.kd_EAST, self.eAvg)
        pitchControl, self.northI = self.PID(errorNorth, self.northPrevError, self.northI, dt, self.kp_NORTH, self.ki_NORTH, self.kd_NORTH, self.nAvg)
        thrustControl, self.downI = self.PID(errorDown, self.downPrevError, self.downI, dt, self.kp_DOWN, self.ki_DOWN, self.kd_DOWN, self.dAvg)
        yawControl, self.yawI     = self.PID(errorYaw, self.yawPrevError, self.yawI, dt, self.kp_YAW, self.ki_YAW, self.kd_YAW, self.yAvg)
        
        # Constrain I terms to prevent integral windup
        self.northI = self.constrain(self.northI, self.northIcontstrain[0], self.northIcontstrain[1])
        self.eastI  = self.constrain(self.eastI, self.eastIcontstrain[0], self.eastIcontstrain[1]) 
        self.downI  = self.constrain(self.downI, self.downIcontstrain[0], self.downIcontstrain[1])
        self.yawI   = self.constrain(self.yawI, self.yawIcontstrain[0], self.yawIcontstrain[1])

        # Update previous error
        self.northPrevError = errorNorth
        self.eastPrevError  = errorEast
        self.downPrevError  = errorDown
        self.yawPrevError   = errorYaw
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

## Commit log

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2019-05-06 Setup full PID controller. Just need to tune. GUIDED_NOGPS not working?
    [main-SITL.py]
2019-05-08 Change to class structure, fix rad and deg conversion, constrain cntrl.
    [main-SITL.py]
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2019-05-10 Create altitude test with hardware. Works on ground, had to flip a few -
    [main.py]
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2019-05-23 Fix controller directions +/- and 2 small variable errors.
    [main.py]
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2019-06-01 Removed data files and images and stored locally.
    [2019-05-24 18:25:14.csv, 2019-05-24 18:35:15.csv, 2019-05-24 18:36:10.csv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]
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2019-06-12 Update yaw value, invert roll and pitch control, print more data.
    [main.py]
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2019-06-14 Add delay and switch trigger order to limit signal interference.
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2019-06-21 Commit data and quick data anlyzing function.
    [firstFlight.csv, secoundFlight.csv]
2019-06-24 Fix the PD controller to PID and make it proper.
    [main-SITL.py]
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2019-06-25 Fix PID controller calls and implmentation.
    [main-SITL.py]
2019-06-25 Fix timeStamp and dt variables
    [main-SITL.py]
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2019-06-27 Remove data and save local.
    [firstFlight.csv, secoundFlight.csv]
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2019-06-27 Bug fixes, update log data, and increase yaw rate from 45 deg/s to 90.
    [main.py]
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2019-06-28 Increase thrust err tolerance, command update to 0.05, cntr RC mappings
    [main.py]
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2019-10-01 Added timeSync back to class due to pointer removal fix.
    [main.cpp]
2019-10-01 Remove old clamp-twist versions for updated manipulatorActuation class.
    [Wiring_Diagram.fzz]
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2019-10-21 Initial commit blank PCB
    [clamp_and_torque.kicad_pcb, clamp_and_torque.sch]
2019-10-21 Commit 75% of initial prototype
    [clamp_and_torque.kicad_pcb]
2019-10-23 Update some footprints and add a few more components.
    [clamp_and_torque.kicad_pcb, clamp_and_torque.sch]
2019-10-24 Cleaned up schematic and roughly placed all components.
    [clamp_and_torque.kicad_pcb, clamp_and_torque.sch]
2019-10-28 Add NRF24L01 pinout to PCB
    [clamp_and_torque.sch]
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2019-10-29 Add current sensor and rename project to follow software branch.
    [cap.kicad_pcb, cap.sch, clamp_and_torque.sch]
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2019-10-30 Layout board ready for autorouting.
    [cap.dsn, cap.kicad_pcb]
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2019-11-19 Debugging errors with hardware for MASTER node.
    [main.cpp]
2019-11-19 Fix incorrect variable names.
    [main.cpp]
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2019-11-20 Changed naming conventions and fixed switch case
    [main.cpp]
2019-11-20 Force only control, fix boundary control, and open state perfect.
    [main.cpp]
2019-11-20 Add deafult error handing case.
    [main.cpp]
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2019-11-26 add example logging data
    [2019-11-26 21:51:05.csv, 2019-11-26 21:51:59.csv]
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2019-12-12 Add marker properties and one error handling case.
    [vision.py]
2019-12-12 Tolerance take off altitude for newest version of Arducopter.
    [main-SITL.py]
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2019-12-12 Fix control ratios and directions.
    [controller.py, main.py]
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2020-02-23 Minor updates to PCB. Push to windows.
    [cap.kicad_pcb, cap.sch]
2020-05-05 Remove PCB's for now.
    [clamp_and_torque.kicad_pcb, clamp_and_torque.sch]
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2020-05-06 Added two current sensing options. Hall and shunt
    [cap.sch]
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2020-05-06 Layed out mjaor components, need to select connectors.
    [cap.kicad_pcb, cap.sch]
2020-05-06 Added Molex connectors and conceptual layout complete
    [cap.kicad_pcb, cap.sch]
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2020-05-06 Roughly MASTER schematic complete w/ footprints
    [MASTER.kicad_pcb, cap.sch]
2020-05-07 Completed approximate layout. Need to route
    [MASTER.kicad_pcb, MASTER.sch]
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2020-05-08 minor tweaks and added completed vibration board - schematic and routing
    [camera.kicad_pcb, vibration.kicad_pcb, vibration.sch]
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2020-05-08 Vibration review complete. Create gerbers
    [vibration-B_Cu.gbr, vibration-B_Mask.gbr, vibration-B_Paste.gbr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]
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2020-05-09 created a frankenstein of a PCB but it had to be done.
    [fluid-B_Cu.gbr, fluid-B_Mask.gbr, fluid-B_Paste.gbr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]
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2020-05-13 Only dispay errors during camera calibration
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2020-05-16 Autofocus=0, fix Pose count
    [vision.py]
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2020-05-16 Fixed arg parse errors for multiple resolutions
    [vision.py]
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2020-05-20 Fix whitespace and old refs to V thread
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2020-05-27 Clean data stream need to fix some error handling
    [main.py]
2020-05-27 Fixed error catch by removing finally & loop.close
    [main.py]
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2020-05-27 Fixed how vision will end with keyboard exception
    [vision.py]
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2020-06-02 Retune yaw: make it a little more snappy
    [controller.py]
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2020-06-02 Minor error fixes from hardware test
    [main.py]
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2020-06-13 FIx controller directions. Yaw appears to be tuned
    [controller.py]
2020-06-13 Make roll and pitch more snappy (2.5x)
    [controller.py]
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2020-06-16 Reset integral term to prevent wind up
    [controller.py, main.py]
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2020-06-16 I need a way to not keep doing this...
    [2020-06-16__21-52-50.csv]
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2020-06-16 Might need to turn gains up. Or dead battery
    [2020-06-16__23-14-16.csv]
2020-06-17 Possible fix for initial mode switch attack issue
    [main.py]
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2020-06-19 Some oscillations in yaw
    [2020-06-19__02-13-15.csv]
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2020-06-19 Fix yaw plot color scheme
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2020-06-22 Turned off filters and took another data set
    [2020-06-22__02-59-06.csv]
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2020-06-23 Fix identation and missing var
    [setpoints.py]
2020-06-23 Fix errors from hardware test
    [filter.py, main.py, setpoints.py]
2020-06-23 Yawing the wrong way i think
    [2020-06-23__21-54-57.csv]
2020-06-23 seems better. might have been a calibration issue
    [2020-06-23__22-19-28.csv]
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2020-06-24 Holding much more stable. Slightly off balanced and some oscillations
    [2020-06-24__02-42-28.csv, 2020-06-24__02-45-41.csv]
2020-06-24 Held for a few seconds super stable then began to oscillate
    [2020-06-24__02-56-16.csv]
2020-06-24 Trajectory gen was smooth, need to fix steady state
    [2020-06-24__03-01-47.csv]
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2020-06-24 Really dropping the yaw is allowing for smoother flight.
    [2020-06-24__17-00-29.csv]
2020-06-24 First landing test. New setpoints and offset on yaw value
    [2020-06-24__17-23-06.csv]
2020-06-24 Fix bug where controller never allowed thrust below 0.5
    [controller.py]
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2020-06-24 Tweak gains more. Holds good for a while then gets knocked around
    [2020-06-24__20-15-45.csv]
2020-06-24 Fix index issue when trajectories are different lengths
    [setpoints.py]
2020-06-24 same trend. Holds good then looses it with distrubances
    [2020-06-24__20-27-58.csv]
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2020-06-24 something odd going on way out of control
    [2020-06-24__21-14-27.csv, 2020-06-24__21-17-00.csv]
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2020-06-25 Fix missing square on sigma E
    [filter.py]
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2020-06-25 Turned off mixer. Second file was okay. Battery voltage dropping
    [2020-06-25__16-39-45.csv, 2020-06-25__16-45-23.csv]
2020-06-25 yaw is still oscillating
    [2020-06-25__17-51-33.csv]
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2020-06-25 Test script to see if gyros are zeroed or drift
    [main.py]
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2020-07-01 Fix matrix dimensional issues
    [vision.py]
2020-07-01 Test with old battery. Broke landing gear
    [2020-07-01__19-13-01.csv, 2020-07-01__19-14-42.csv]
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2020-07-01 Flip the frame
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2020-07-01 slightly more responisve with solder fix
    [2020-07-01__21-47-20.csv]
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2020-07-01 Offset was a big fix. This worked decent
    [2020-07-01__21-59-38.csv, 2020-07-01__22-10-05.csv]
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2020-07-12 Increase allowable angle. Some oscillations
    [2020-07-12__16-53-17.csv, 2020-07-12__16-55-25.csv]
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2020-07-12 Look at setting gains back 2 what they were
    [2020-07-12__17-20-19.csv]
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2020-07-19 Fix to correct coordiante systems and angles
    [vision.py]
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2020-07-20 Flight data with low pass and no kalman
    [2020-07-20__02-41-22.csv]
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2020-07-20 First landing attempt. so close at the end
    [2020-07-20__02-52-55.csv]
2020-07-20 Changed some gains and set point. Low battery
    [2020-07-20__02-57-55.csv]
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2020-07-21 Missed one
    [2020-07-20__03-27-15.csv]
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2020-07-22 Fix direction for pitch
    [controller.py]
2020-07-22 Direction fix did wonders. Decent flight
    [2020-07-22__02-10-57.csv]
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2020-07-22 Yaw turned way down. Why does it wonder?
    [2020-07-22__02-23-37.csv]
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2020-07-22 Pretty decent flight. Think that ESC needs to be changed
    [2020-07-22__02-45-09.csv, 2020-07-22__02-47-56.csv]
2020-07-22 Pretty solid flight. Travels a bit but makes a recovery
    [2020-07-22__02-54-50.csv]
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2020-07-22 not landing where it needs to. Might be loosing target
    [2020-07-22__03-56-26.csv, 2020-07-22__03-59-34.csv]
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2020-07-22 FC had a weird thing happen. Had to restart 3 times
    [2020-07-22__22-12-19.csv]
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2020-07-22 0.2, 0.02, 0 integral term. Last one was good but crashed
    [2020-07-22__23-15-36.csv, 2020-07-22__23-18-19.csv, 2020-07-22__23-20-41.csv]
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2020-08-09 Fixed mixer with SITL
    [controller.py]
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2020-08-11 Removed C920 and replaced with T265
    [vision.py]
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2020-08-12 Update to 11x17 marker, fix some error handling
    [vision.py]
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2020-08-13 Reset the timer
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2020-08-20 getting so close. Battery swap
    [2020-08-20__16-45-01.csv, 2020-08-20__16-48-22.csv, 2020-08-20__16-50-48.csv]
2020-08-20 the first one matches close video. Need to add I
    [2020-08-20__16-57-26.csv]
2020-08-20 Maybe turn p back down... Double checking home position
    [2020-08-20__16-59-50.csv, 2020-08-20__17-02-19.csv]
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2020-08-21 bad crash
    [2020-08-20__19-19-00.csv]
2020-08-21 Decrease P down gain after the fatal crash. Sad.
    [controller.py]
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2020-08-23 first one closest yet, 2nd one no tray
    [2020-08-22__21-25-56.csv, 2020-08-22__21-27-57.csv, 2020-08-22__21-30-26.csv]
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2020-08-25 control is stable but UAV internal loop seems off
    [2020-08-24__21-03-18.csv, 2020-08-24__21-06-04.csv]
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2020-08-25 keeps drifting
    [2020-08-24__21-42-53.csv, 2020-08-24__21-44-46.csv]
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2020-08-25 Increase trajectory by 2 seconds and acc0 added
    [2020-08-24__21-58-50.csv]
2020-08-25 very stable first flight. Just off by a little
    [2020-08-25__12-35-19.csv]
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2020-08-25 reduce gain height to zero and reduce east
    [2020-08-25__12-54-22.csv]
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2020-08-26 How does the D term make it better
    [2020-08-25__18-31-08.csv, Gains-2020-08-25__18-31-07.csv]
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2020-08-27 somewhat unstable
    [2020-08-27__15-17-15.csv, Gains-2020-08-27__15-17-15.csv]
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2020-09-02 crash and boom
    [2020-09-02__16-26-16.csv, Gains-2020-09-02__16-26-15.csv]
2020-09-03 Fix mode switch bug with wave test
    [main.py]
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2020-09-08 Just time stabilize and rpy print
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2020-09-09 Profile data for 20 W power supply. No kalman
    [2020-09-09__17-25-10.csv, Gains-2020-09-09__17-25-08.csv]
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2020-09-10 Bug fix pos and vel mixup
    [main.py]
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2020-09-11 Fix dt. Getting 33.3 +/- 3 ms as only process
    [T265.py]
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2020-09-12 Fix up kalman filter script
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2020-09-13 Fix timeout from non blocking to 1s timeout
    [payloads.py]
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2020-09-20 Save previous time and prevent loop r8 blowing up
    [filter.py]
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2020-09-20 Increase yaw wave to 30 deg / s
    [CONTROL-2020-09-19__21-52-35.csv, CONTROL-2020-09-19__21-59-41.csv, MAIN-2020-09-19__21-52-35.csv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]
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2020-09-24 Add trim switch, turned off GPS, & fixd a failsafe
    [Parameters.params]
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2020-09-25 get those oscillations
    [2020-09-24__18-24-03--CONTROL.csv, 2020-09-24__18-24-03--MAIN.csv]
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2020-09-27 had some issues with trim on manual control
    [2020-09-26__20-22-19--CONTROL.csv, 2020-09-26__20-22-19--MAIN.csv]
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2020-09-28 Fix initial state for landing
    [main.py]
2020-09-28 unstable start
    [2020-09-28__15-58-37--CONTROL.csv, 2020-09-28__15-58-37--MAIN.csv]
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2020-09-28 Some sampling freq issue but good flight
    [2020-09-28__16-18-00--CONTROL.csv, 2020-09-28__16-18-00--MAIN.csv]
2020-09-28 Try and prevent jump at very start
    [controller.py]
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2020-09-29 Test flight same gains but with low pass filter on D
    [2020-09-28__19-22-13--CONTROL.csv, 2020-09-28__19-22-13--MAIN.csv]
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2020-09-29 Fix order of data logging
    [controller.py]
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2020-09-29 fixed constraining thing
    [2020-09-28__20-42-34--CONTROL.csv, 2020-09-28__20-42-34--MAIN.csv]
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2020-10-19 up P again for oscillations
    [2020-10-18__18-45-32--CONTROL.csv, 2020-10-18__18-45-32--MAIN.csv]
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2020-10-19 change D filter window from 5 to 3
    [2020-10-18__22-12-21--CONTROL.csv, 2020-10-18__22-12-21--MAIN.csv]
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2020-10-19 low battery but seemed 2 snappy
    [2020-10-18__22-29-06--CONTROL.csv, 2020-10-18__22-29-06--MAIN.csv]
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2020-10-22 Swap r and g LED, add serial debug
    [main.cpp]
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2020-10-23 Fix current reading returns
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2020-10-30 Reset values to nominal
    [controller.py, main.py]
